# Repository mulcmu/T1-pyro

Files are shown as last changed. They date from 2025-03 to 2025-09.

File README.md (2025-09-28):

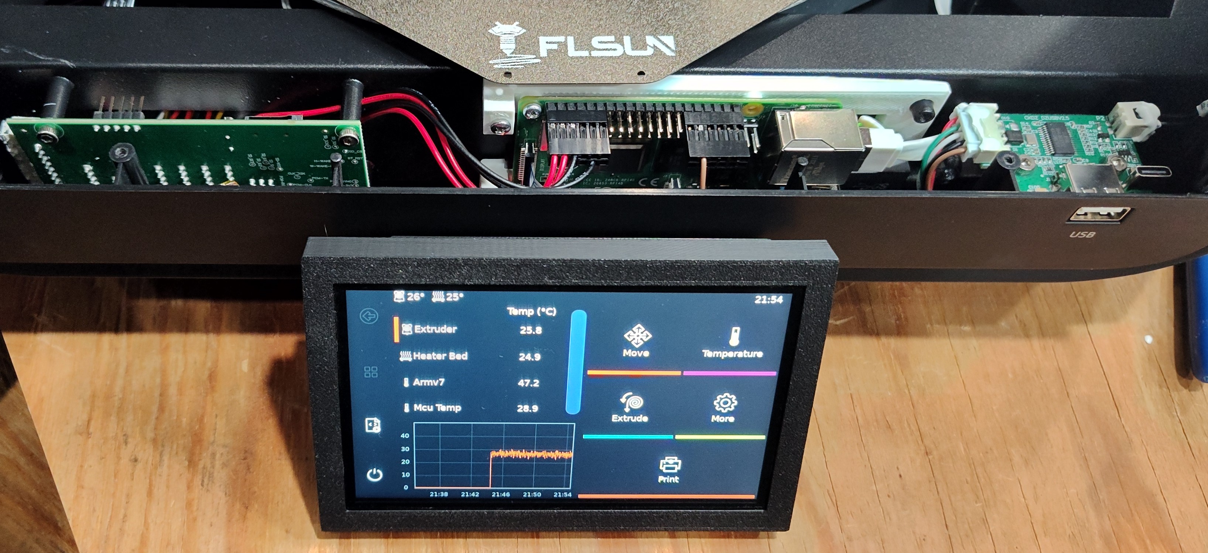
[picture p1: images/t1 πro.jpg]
./images/t1 πro.jpg


# T1 πro
Document and share progress to convert a FLSUN T1 Pro to T1 πro.

### Objectives

- Replace the stock host board (Core Board) with a Raspberry Pi
- Replace the stock screen with Fysetc Raspberry Pi 5 inch DSI Display
- Document stock hardware connections for troubleshooting/upgrades
- Reuse other stock hardware as much as practical
- Clean installation
- Up to date OS and Klipper [Ecosystem](https://klipper.discourse.group/t/klipper-architecture-ecosystem/6313)

### Current Status

* Pi 4 and the screen installed, fully operational
* Uses the stock 5v power supply on lower adapter board for Pi
* USB camera hub board reused by Pi
* Currently <u>irreversible</u> after flashing Klipper MCU hardware 
* [[load cell]](https://github.com/garethky/klipper/tree/load-cell-probe-community-testing) community testing branch working with stock lower function adapter board
  * `before: range 0.046875, average -0.420110, stDev 0.010482, average delta: 0.011671`
  * `  after: range 0.002557, average -0.304737, stDev 0.000692, average delta: 0.000532`

* Macros need a lot of work
* Help wanted, contributions welcomed

### Gen1/Gen2 Stock Hardware

My original T1 Pro was a Gen2, second T1 Pro purchased opened box was Gen1.  The Gen1 has older revision PCBs.  The Gen1 motherboard came with BTT stepper drivers vs FLSUN brand on Gen2.  BTT silk screen painted over in green even though the spare part clearly displayed the BTT marking on the website.  The Gen2 motherboard has some changes from the Gen1, Gen1 lacks the 5 pin firmware download header and a bunch of transistors under the steppers.  Gen1 has  some pin header jumpers under the steppers that are not on Gen2.  

The lower function adapter board on Gen1 has the low noise ADC chip bodged onto the back of the PCB and held with copious amounts of the white silastic.

The Gen2 CPAP fan aligned with the air hole opening in the top cover.  The Gen1 did not and sucked air in from inside the enclosure.

Gen1 also looks to have an older effector pcb, haven't taken that apart yet to document.

### Differences

* Fully open source Klipper ecosystem
* No power loss protection
* Ethernet connection possible, not just wifi
* Slightly bigger screen with more control
* Potential for Load cell probe accuracy improvements

### TODO

- [ ] Cleanup the printer.cfg file and macros
- [ ] Create Schematic (in progress)
- [X] Trace motor SPI connections
- [x] Document lower adapter board
- [x] Fix lower adapter board usart1 rx/tx
- [x] Document effector PCB and determine cable pinout
- [x] Document πro custom cables
- [X] Hotend thermistor noise at ambient temps
- [ ] Cleanup katapult installation
- [ ] Make a scripts for mcu fw compile and katapult deploy
- [X] moonraker [timelapse](https://github.com/mainsail-crew/moonraker-timelapse/blob/main/docs/installation.md)
- [ ] Document modifications to improve bed probe [performance](https://klipper.discourse.group/t/load-cell-probing-algorithm-testing/9751/102)
- [ ] Slay underbed dragons (potential regions were probe will not trigger as two load cells readings are exactly balanced out by 3rd load cell reading)
- [X] Modification for filament <u>movement</u> sensor
- [X] Better camera (mine broke already)
- [ ] Chamber temperature, RH, sensor
- [ ] Chamber heater support
- [ ] Improve boot speed of Pi
- [X] Does Pi need heatsinks or extra cooling - YES
- [ ] Overlay file system or similar to make more robust to power loss
- [ ] Installation guides
- [ ] Logo
- [ ] Standard preinstalled Pi image
- [ ] Redesign the screen bracket
- [ ] Find stock firmware for the motherboard MCU
- [x] Stock firmware for the probe MCU

### STL Models

Fusion360 models and STL located on pintables:

* https://www.printables.com/model/1191414-flsun-t1-pro-pi-and-screen-bracket
* https://www.printables.com/model/1282464-flsun-t1-alternate-camera
* https://www.printables.com/model/1401304-flsun-t1-vent-hole-drill-guide
* https://www.printables.com/model/1282464-flsun-t1-alternate-camera

### Custom Cables

* Custom cable from a Pi usb connector to the stock Usb hub board
* Custom cable from the stock lower adapter board 5v to the Pi *GPIO*
* [Details](custom_cables.md)

### Parts

* USB Extension cable for MCU ([Type A male to Type C female](https://www.amazon.com/dp/B07M999Y6T))
* Optional for Ethernet 
  * Low profile [connector cable](https://www.amazon.com/dp/B0D9JVSB2X?ref_=ppx_hzsearch_conn_dt_b_fed_asin_title_1) 
  * [Bulkhead connector](https://www.amazon.com/dp/B0D9JVSB2X)
* Industrial / rugged SD card for Pi
* SD card for flashing upper core board firmware
* ST Link v2 clone or similar [SWD debugger](https://github.com/WeActStudio/WeActStudio.MiniDebugger) (Required for [load_cell], recommended for katapult install on motherboard MCU)
* Some assorted M2, M2.5 and M3 screws are needed for assembly

### Installation

Current high level guide to implement:

* Get Pi setup and Klipper installed and tested before physical install into machine
* Print the brackets for printer installation
* Make the custom cables
* Remove stock host PCB (Core board) and screen
* Install Pi and 5" screen
* Flash Klipper firmware to motherboard
* [Optional for load cell] Modify lower function board with jumper and flash Klipper firmware to lower function board

Details:

* Fresh Bookworm Install:  Use Raspberry Pi Imager software to install Raspberry Pi OS Lite (64-bit)  to the SD card
    Current release is 2025-05-13.  Tested with 2024-11-19.

* Edit settings to set desired host name, password, and wifi configuration

* Modify the Pi config.txt

    ```
    # Uncomment some or all of these to enable the optional hardware interfaces
    dtparam=i2c_arm=on
    #dtparam=i2s=on
    #dtparam=spi=on
    
    # Enable audio (loads snd_bcm2835)
    dtparam=audio=on
    
    # Enable pwmchip sysfs interface
    dtoverlay=pwm-2chan,pin=12,func=4,pin2=13,func2=4
    
    # Automatically load overlays for detected cameras
    camera_auto_detect=0
    
    # Automatically load overlays for detected DSI displays
    display_auto_detect=1
    
    # Automatically load initramfs files, if found
    auto_initramfs=1
    
    # Don't have the firmware create an initial video= setting in cmdline.txt.
    # Use the kernel's default instead.
    disable_fw_kms_setup=1
    
    # Run in 64-bit mode
    arm_64bit=1
    
    # Disable compensation for displays with overscan
    disable_overscan=1
    
    # Run as fast as firmware / board allows
    arm_boost=1
    
    [cm4]
    otg_mode=1
    
    [cm5]
    dtoverlay=dwc2,dr_mode=host
    
    [all]
    enable_uart=1
    ```

> [!NOTE]
>
> Potential issues with touchscreen and [wifi firmware](https://github.com/KlipperScreen/KlipperScreen/discussions/1491).  I did not encounter any issues with the wifi.
>
> ``` Remove problematic wifi
> sudo apt remove firmware-brcm80211
> sudo apt-mark hold firmware-brcm80211
> sudo reboot now 
> ```

* First boot, use SSH or usb keyboard to update

  ``` 
  sudo apt update
  sudo apt upgrade
  sudo systemctl disable systemd-networkd-wait-online.service
  sync
  sudo reboot now
  ```

* Install ts_lib for touch calibration

  ```
  sudo apt-get install libts-bin
  sudo ts_calibrate
  sudo ts_test
  sync
  sudo reboot now
  ```

* Install Git, KIAUH, Klipper, moonraker, mainsail, klipperscreen, crowsnest, klipper-backup, 

    ```
    sudo apt-get install git
    cd ~ 
    git clone https://github.com/dw-0/kiauh.git
    ./kiauh/kiauh.sh
    ```

* Optional for [load_cell] support: switch to load-cell-probe-community-testing fork

    ```	
    echo "For KIAUH v5"
    cd ~/kiauh
    nano klipper_repos.txt
    
    echo "For KIAUH v6"
    cp default.kiauh.cfg kiauh.cfg
    nano kiauh.cfg
    ```

	add this to file and save:

   ```
   https://github.com/garethky/klipper,load-cell-probe-community-testing
   ```

	switch klipper branch in kiauh to the load cell testing repository

* Install extra python packages for Measuring Resonances and Load_Cell

  ```
  sudo apt install python3-numpy python3-matplotlib libatlas-base-dev libopenblas-dev python3-scipy python3-serial
  ~/klippy-env/bin/pip install -v "numpy<1.26"
  ~/klippy-env/bin/pip install -v "scipy"
  ```

* Optional for [load_cell] support: Setup load cell [probe debug tool](https://observablehq.com/@garethky/klipper-load-cell-debugging-tool)

* Install ST-Link

  ```
  sudo apt install gcc build-essential cmake libusb-1.0-0 libusb-1.0-0-dev libgtk-3-dev pandoc -y
  cd ~ 
  git clone https://github.com/stlink-org/stlink.git
  cd stlink
  make clean && make release
  sudo make install
  sudo ldconfig
  ```

* Install katapult

    ```
    cd ~
    git clone https://github.com/Arksine/katapult
    ```

* Install timelapse

    ```
    cd ~/
    git clone https://github.com/mainsail-crew/moonraker-timelapse.git
    cd ~/moonraker-timelapse
    make install
    
    ```

    ```
    # moonraker.conf
    
    [update_manager timelapse]
    type: git_repo
    primary_branch: main
    path: ~/moonraker-timelapse
    origin: https://github.com/mainsail-crew/moonraker-timelapse.git
    managed_services: klipper moonraker
    ```

* No login shell (required for load_cell) and Wifi enabled (optional)

    ``` 
    sudo raspi-config
    ```

    * Setup wifi under System Options
    * Select wifi country in Localizations Options
    * Enable serial uart, no console
      * Interface options
      * Serial Port
      * No login shell
      * Yes hardware enabled
    ```
    sudo nmtui
    ```

    * Check wifi setup and add additional networks if desired

* Enable host mcu
  * Setup hardware PWM using this guide https://www.klipper3d.org/RPi_microcontroller.html
  
  * The case light gets connected to PWM0 with it routed it to gpio12.
  
  * /etc/rc.local will need to be created, don't forget the #! and chmod +x
  
    ```
    #!/bin/sh -e
    
    # Enable pwmchip sysfs interface
    echo 0 > /sys/class/pwm/pwmchip0/export
    echo 1 > /sys/class/pwm/pwmchip0/export
    
    exit 0
    ```

* Modify printer.cfg
  * Copy the printer.cfg from this repository and update with your existing calibration (endstops, bedmesh, PID, etc)
  * or.. edit your printer.cfg to remove all the FLSUN additions

* Build motherboard MCU firmware

    ```
    sudo service klipper stop
    cd ~
    cd klipper
    make clean
    cp ~/motherboard.menu.config .config
    make menuconfig
    make
    cp out/klipper.elf ~/motherboard.elf
    cp out/klipper.bin ~/motherboard.bin
    ./scripts/update_mks_robin.py out/klipper.bin ~/Robin_nano35.bin
    cp .config ~/motherboard.menu.config
    sudo service klipper start
    ```

> [!NOTE]
>
> Motherboard MCU menuconfig settings:
>
> * Enable extra low-level configuration options
> * Micro-controller Arch (STM32)
> * Processor model (STM32F103)
> * Bootloader offset (28KiB Bootloader) for SD card flash
> * Bootloader offset (8KiB bootloader) for Katapult
> * Clock Reference (8 MHz)
> * Communication interface (Serial (on USART3 PB11/PB10))
> * (250000) Baud for serial port
> * Enable step on both edges
> * PE8 (pins at startup for heatsink cooling fan until klipper boots)

> [!NOTE]
>
> The Robin_nano35.bin is only for using on SD card with motherboard stock bootloader.

* Optional for load cell support: Build lower function adapter board MCU firmware

  ```
  sudo service klipper stop
  cd ~
  cd klipper
  make clean
  cp ~/load_cell.menu.config .config
  make menuconfig
  make
  cp out/klipper.elf ~/load_cell.elf
  cp out/klipper.bin ~/load_cell.bin
  cp .config  ~/load_cell.menu.config
  sudo service klipper start
  ```

> [!NOTE]
>
> Load Cell MCU menuconfig settings:
>
> * Enable extra low-level configuration options
>
> * Micro-controller Arch (STM32)
>
> * Processor model (STM32F103)
>
> * Bootloader offset (8KiB Bootloader)
>
> * Clock Reference (8 MHz)
>
> * Communication interface (Serial (on USART1 PA10/PA9))
>
> * (250000) Baud for serial port
>
>   

* Build Katapul bootloaders

```
sudo service klipper stop
cd ~
cd katapult
make menuconfig
make clean
make
cp out/katapult.elf ~/mb_katapult.elf
cp out/katapult.bin ~/mb_katapult.bin
sudo service klipper start
```

> [!NOTE]
>
> * Micro-controller Arch (STM32)
> * Processor model (STM32F103)
> * Deployment app (Do not build)
> * Clock Reference (8 MHz)
> * Communication interface (Serial (on USART3 PB11/PB10))
> * Application start offset (8KiB bootloader)
> * (250000) Baud for serial port
> * (!PD12) Status LED:  Optional will turn on led by SD card but will direct short if an SD card is inserted!!!

```
sudo service klipper stop
cd ~
cd katapult
make menuconfig
make clean
make
cp out/katapult.elf ~/lc_katapult.elf
cp out/katapult.bin ~/lc_katapult.bin
sudo service klipper start
```

> [!NOTE]
>
> * Micro-controller Arch (STM32)
> * Processor model (STM32F103)
> * Deployment app (Do not build)
> * Clock Reference (8 MHz)
> * Communication interface (Serial (on USART1 PA10/PA9))
> * Application start offset (8KiB bootloader)
> * (250000) Baud for serial port

* Make custom cables

* Print custom brackets

* Install pi in custom bracket (four M2.5x6 screws)

* Install screen in custom bracket

* Remove the stock screen, host (core board) PCB, ribbon cable on lower adapter board, power cable from lower adapter board, cable from the usb hub

* Optional for load cell support:

    * Remove the J20 5 pin header pins and replace with right angle head pins on bottom of pcb if room

    * A magnet/enamel wire needs added to jumper Pin 30 on STM32F103 to Pin 32

* Install the PI, slide over existing standoffs, secure with two M3x6 screws

* Connect usb adapter extension from pi to the usb cable running to upper adapter board / motherboard

* Connect custom usb hub cable to pi usb and gpio

* (Optional) Connect ethernet cable and fit the bulkhead adapter somewhere.

* Connect the custom power cable from lower adapter board to GPIO

* Initial test, at this point pi and screen should boot when printer turned on.  Klipperscreen should load and show *MCU Protocol Error*.  The MCU firmware needs to be updated (or potentially Klipper downgraded) to be be compatible.

> [!WARNING]
>
> After flashing the Klipper MCU firmware returning printer to original stock configuration is not possible!
* Flash motherboard MCU
  * Copy the ~/klipper/out/Robin_nano35.bin file to an empty fat32 formatted sd card
  * With printer powered off, install the sd card in the motherboard
  * Power on printer and wait 30 seconds
  * Power off printer and remove the sd card
  * Robin_nano35.bin should be renamed to Robin_nano35.cur

* Optional for [load_cell] support: Use ST-Link v2 programmer or similar to flash the load_cell.bin firmware to the STM32
  * Configure [openocd](https://openocd.org/), [stlink tools](https://github.com/stlink-org/stlink), or similar for your programming adapter and OS
  * Connect STLINK v2 adapter to JTAG port on lower function adapter board
  * Save a copy of the existing firmware `st-flash read out.bin 0x0800000 0x20000`
  * Write the load_cell.bin file to the MCU `st-flash write load_cell.bin 0x08000000`

### TODO: katapult stuff

```

sudo service klipper stop
python3 ~/katapult/scripts/flashtool.py --request-bootloader -d /dev/serial/by-id/usb-1a86_USB_Serial-if00-port0
python3 ~/katapult/scripts/flashtool.py -d /dev/serial/by-id/usb-1a86_USB_Serial-if00-port0 -f ~/motherboard.bin
sudo service klipper start

sudo service klipper stop
python3 ~/katapult/scripts/flashtool.py --request-bootloader -d /dev/ttyS0
python3 ~/katapult/scripts/flashtool.py -d /dev/ttyS0 -f ~/load_cell.bin
sudo service klipper start

st-flash erase
st-flash write mb_katapult.bin 0x08000000
st-flash write motherboard.bin 0x08002000

st-flash erase
st-flash write lc_katapult.bin 0x08000000
st-flash write load_cell.bin 0x08002000

host MCU update
sudo service klipper stop
make flash
sudo service klipper start

```

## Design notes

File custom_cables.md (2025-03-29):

To build these cables you need crimpers for Dupont and JST XH terminals, terminals to crimp and the housings.

https://www.amazon.com/YMYP-JST-XH-0-25-1-5mm%C2%B2-JST-SM2-54-Connector/dp/B0C6DKZC4K/ 

https://www.amazon.com/WOWOONE-620pcs-Connector-Housing-Terminal/dp/B0897KGG59/

### Cable from Pi USB to stock USB hub board

The camera and external usb stock pcb uses a usb hub IC.  There is also a transistor circut to power the case light on and off.  The 5 pin 2.54 JST XH connector needs to be wired to one of the Pi's usb ports and the control line for the light connected to the PI GPIO header.

Usb breakout pcb

https://www.amazon.com/MakerHawk-Adapter-Converter-Interface-Breakout/dp/B07MBSTZYG

https://www.amazon.com/Teansic-Breakout-Adapter-2-54mm-Module/dp/B09ZNK2Q5L

Connections

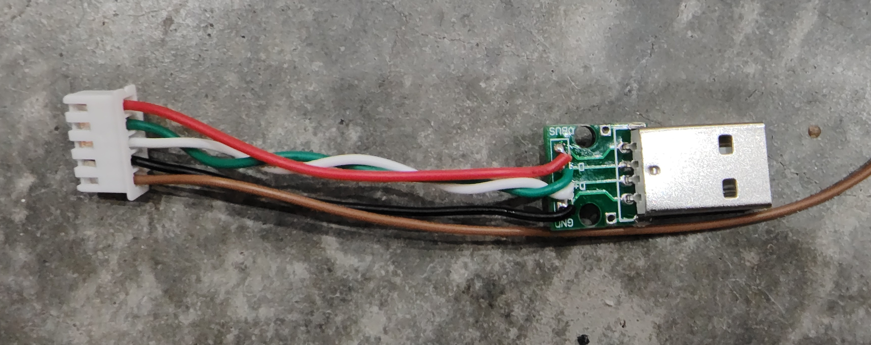
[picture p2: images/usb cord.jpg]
./images/usb cord.jpg


The brown wire goes off to the GPIO Dupont connector.

Use some heat shrink tubing to clean up/protect the usb pcb

Green and white data lines twisted for good measure

### Power Cable

The lower core board has a 5v supply that powered the original motherboard.  There is not enough room to power the Pi via the usb connector when installed so it needs to be powered by the GPIO header.

One side has another 5 pin 2.54 JST XH connector.  The other side needs dupont terminals.  A double row dupont connector 2x6 is recommended for convivence and to keep from messing up the connections.

Two red wires are the 5v and two black wires are the common.

Connections

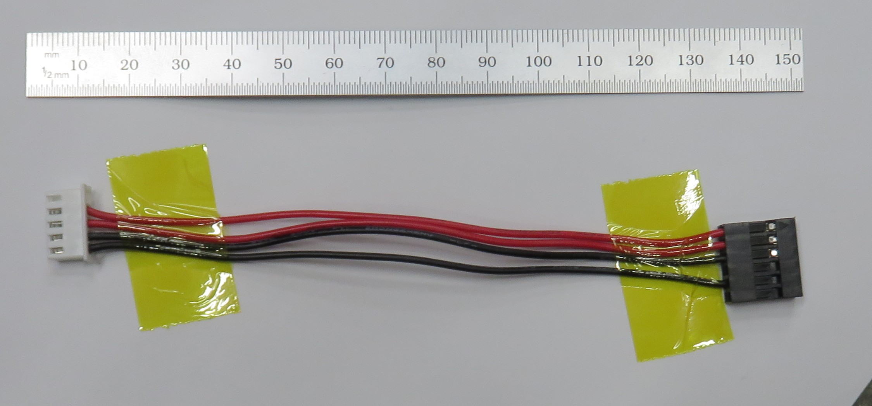
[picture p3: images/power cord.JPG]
./images/power cord.jpg


Optional for [load cell] support:

Two wires need run from the PI GPIO RX/TX to the modified lower function adapter board.  These wires terminate in a separate 5 pin Dupont housing.

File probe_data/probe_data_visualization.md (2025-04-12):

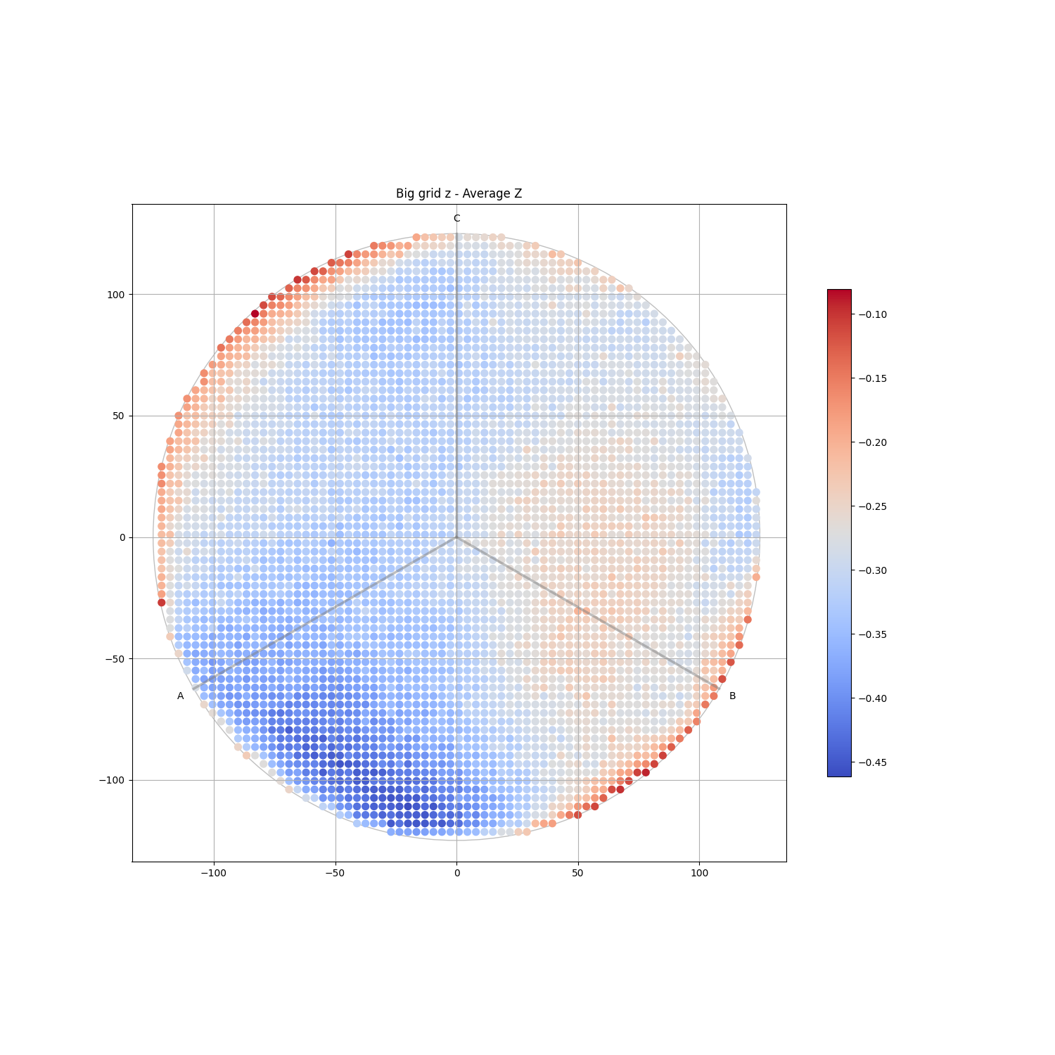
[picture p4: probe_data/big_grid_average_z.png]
Big grid z - Average Z


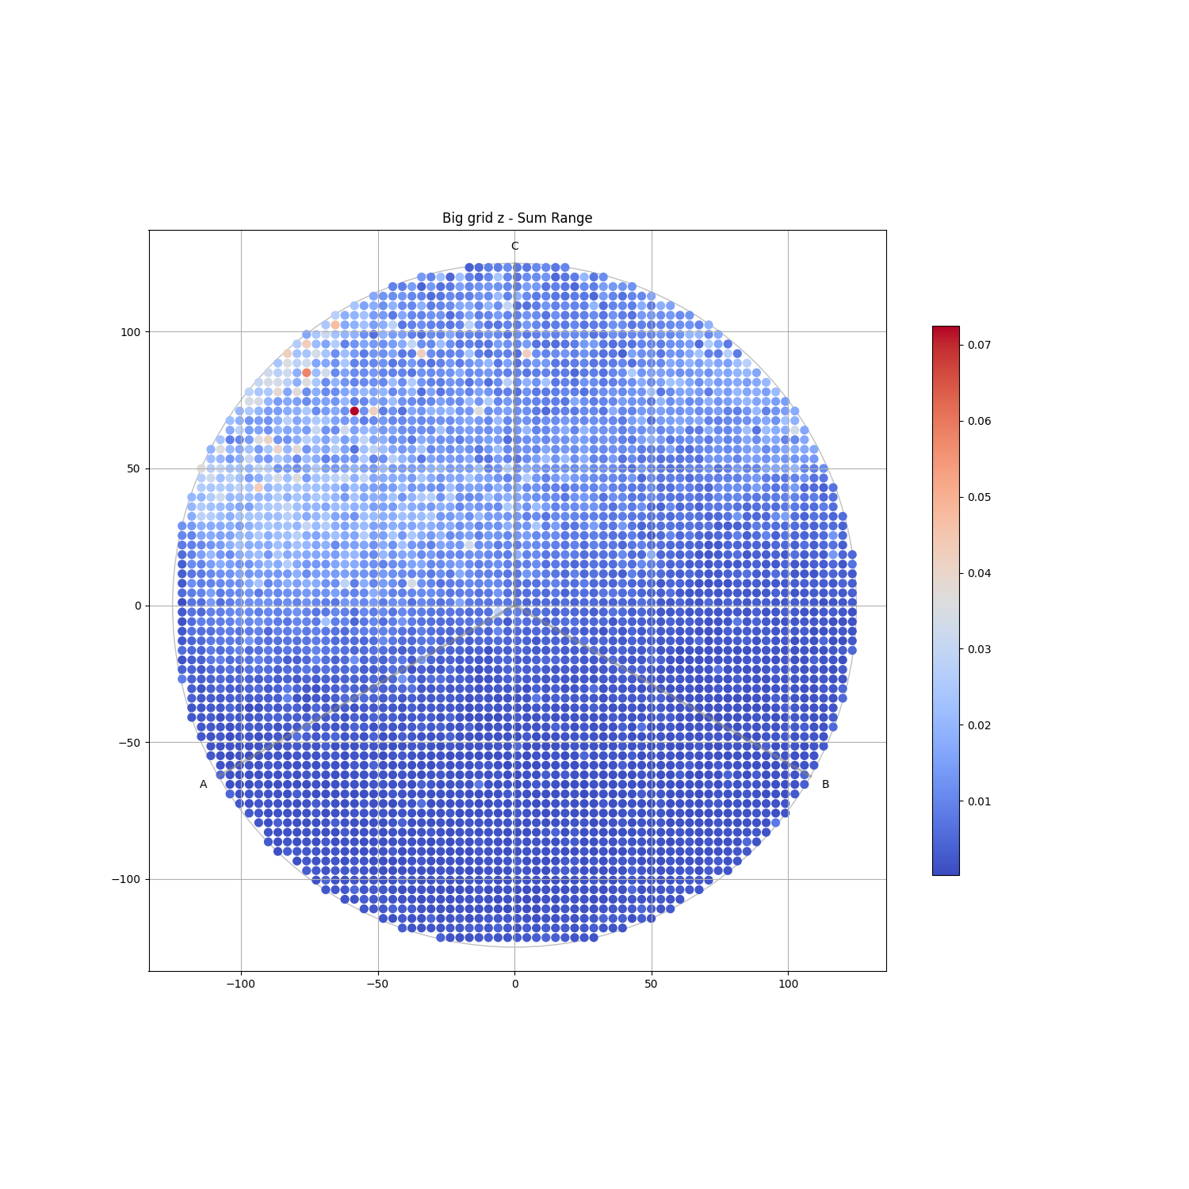
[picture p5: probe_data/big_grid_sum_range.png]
Big grid z - Sum Range


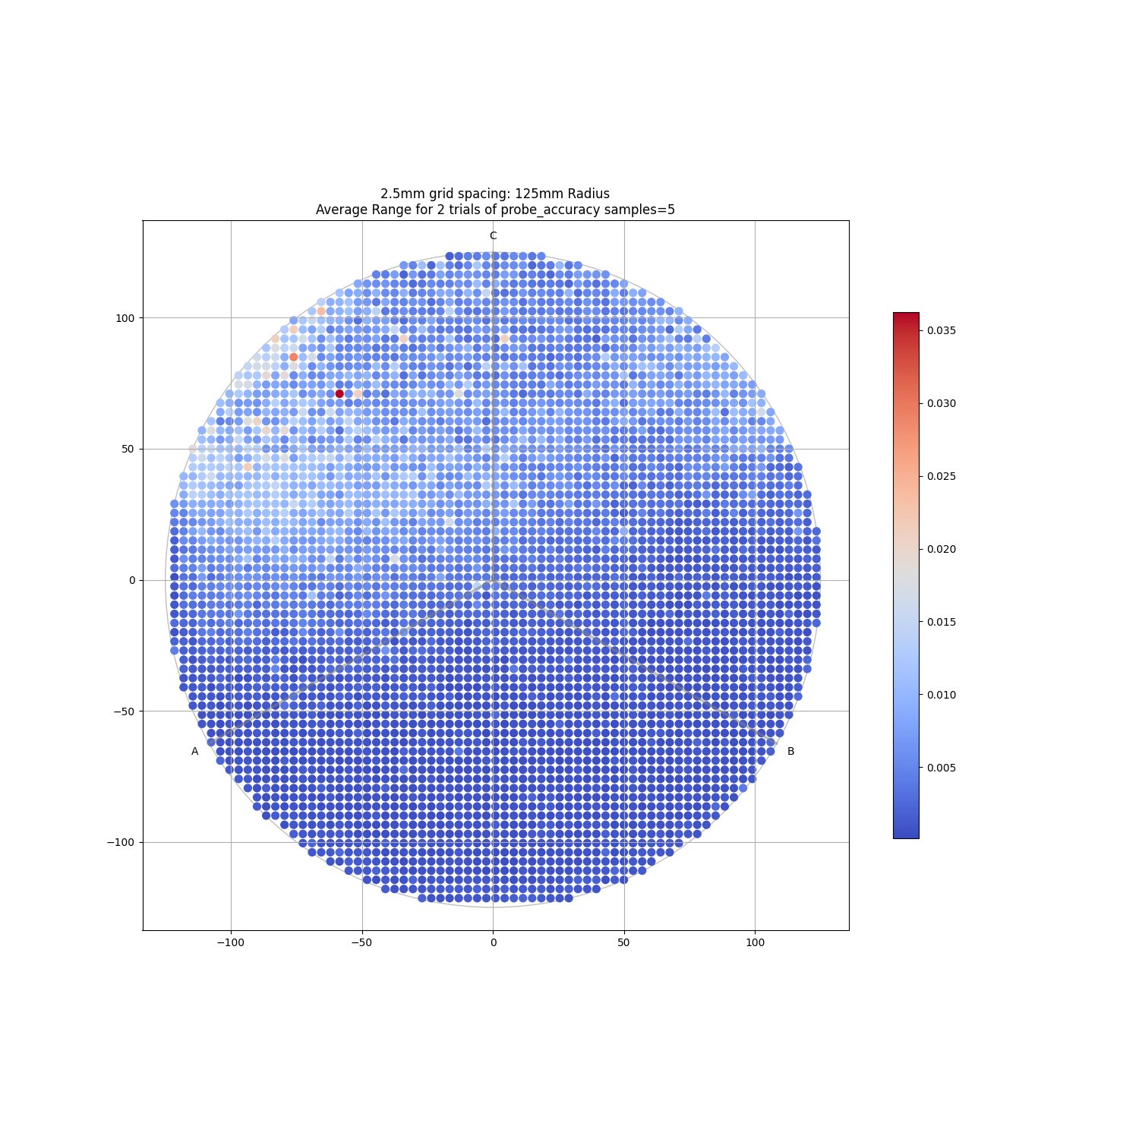
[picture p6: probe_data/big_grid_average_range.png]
2.5mm grid spacing: 125mm Radius Average Range for 2 trials of probe_accuracy samples=5


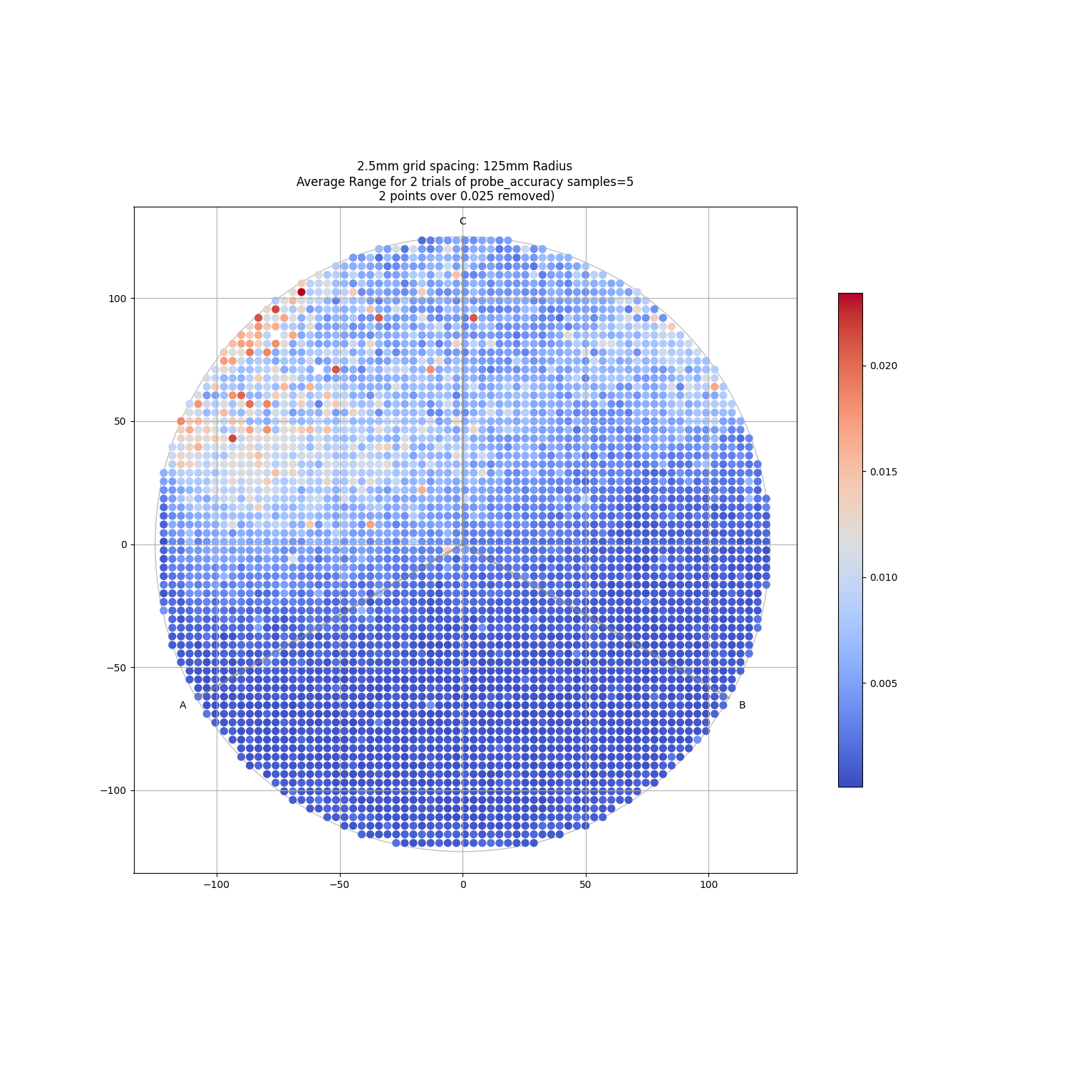
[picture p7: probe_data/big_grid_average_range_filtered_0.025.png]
2.5mm grid spacing: 125mm Radius Average Range for 2 trials of probe_accuracy samples=5 points over 0.025 removed


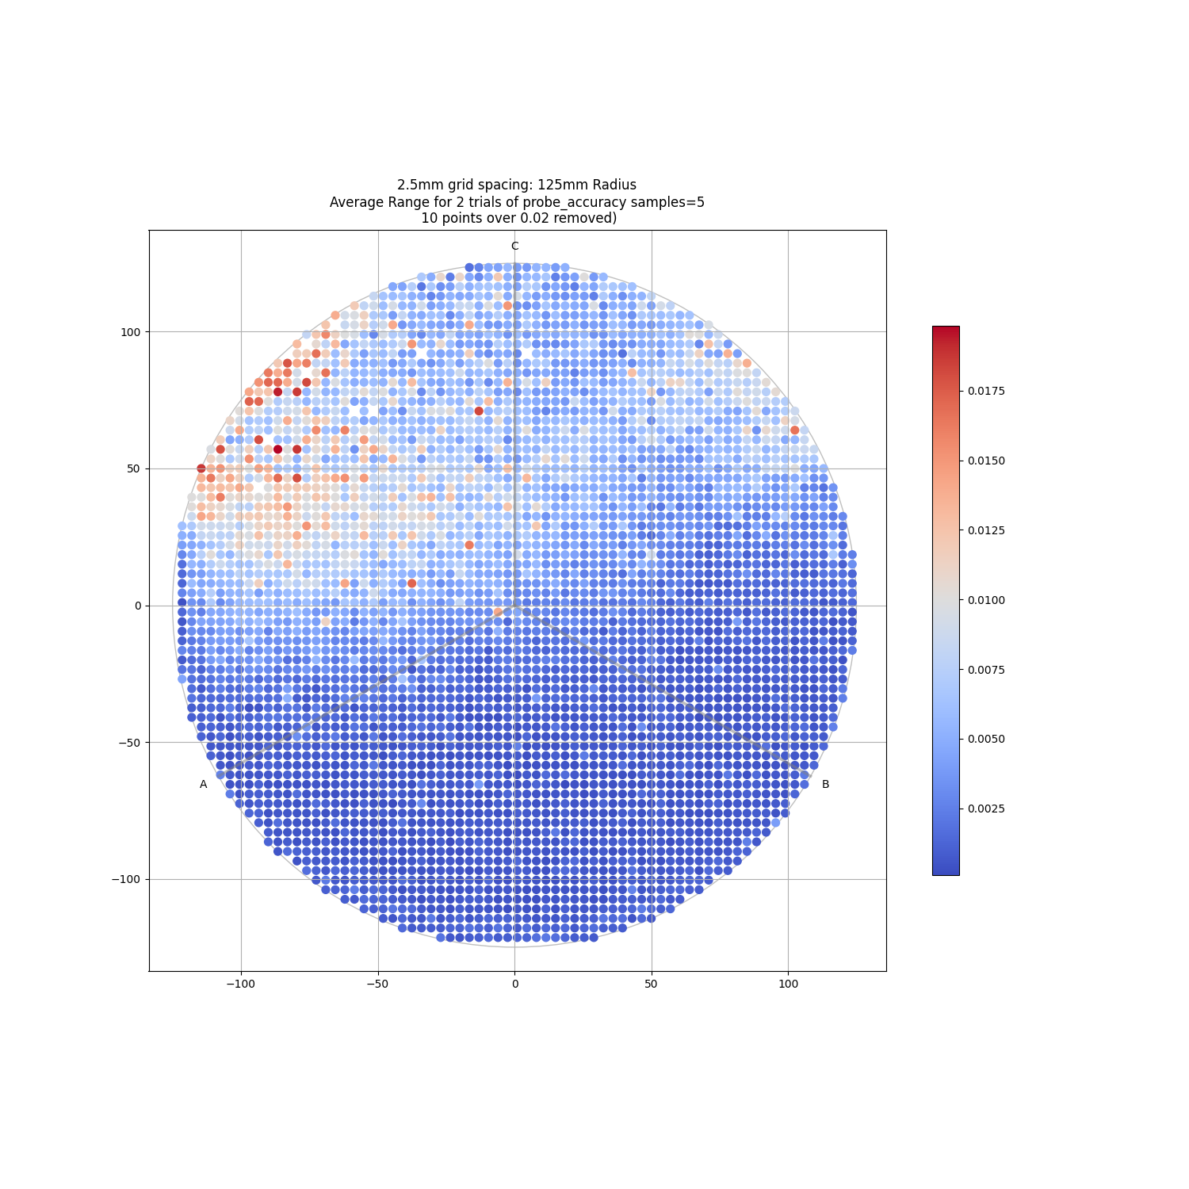
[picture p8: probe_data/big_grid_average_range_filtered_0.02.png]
2.5mm grid spacing: 125mm Radius Average Range for 2 trials of probe_accuracy samples=5 points over 0.02 removed


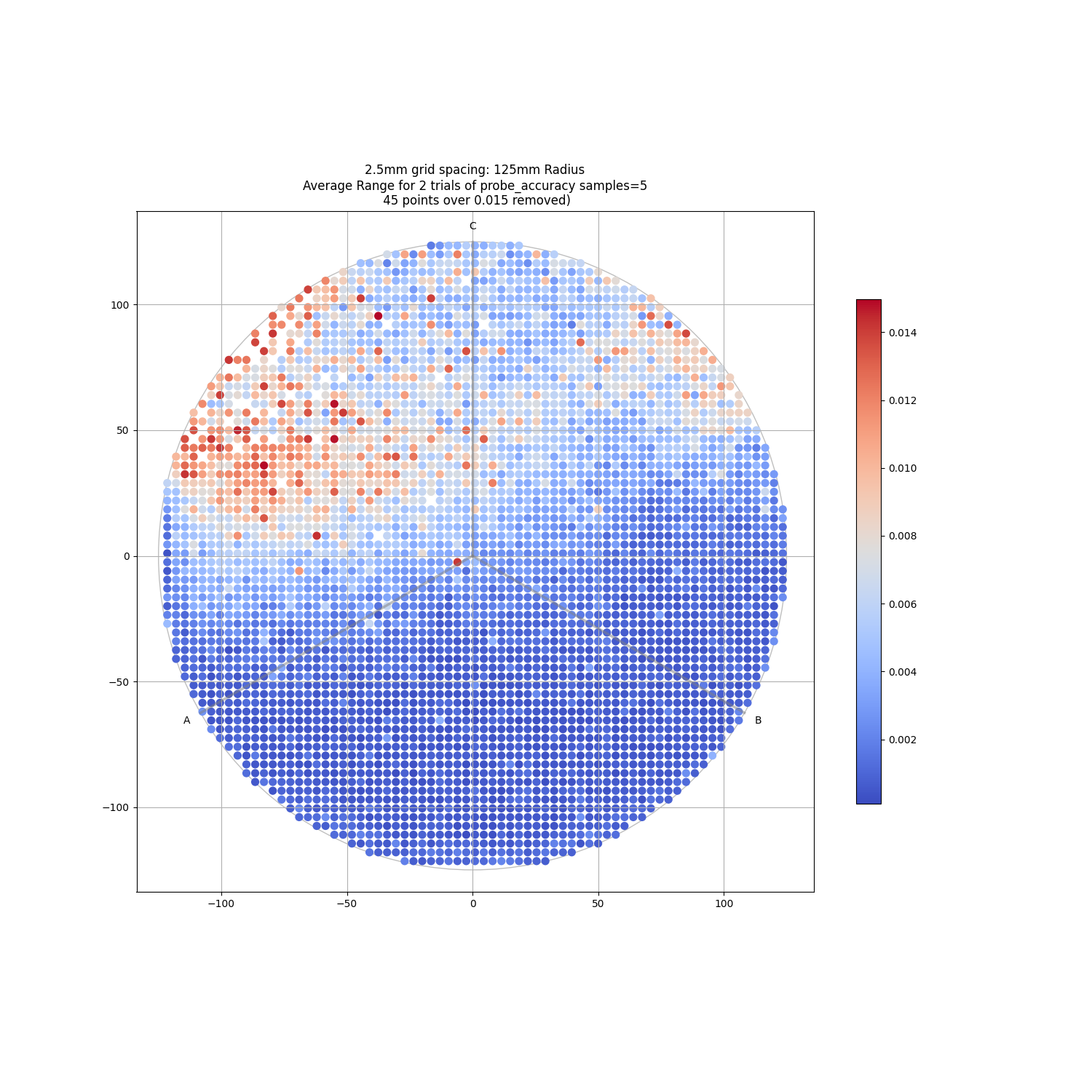
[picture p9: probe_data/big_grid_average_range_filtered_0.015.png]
2.5mm grid spacing: 125mm Radius Average Range for 2 trials of probe_accuracy samples=5 points over 0.015 removed


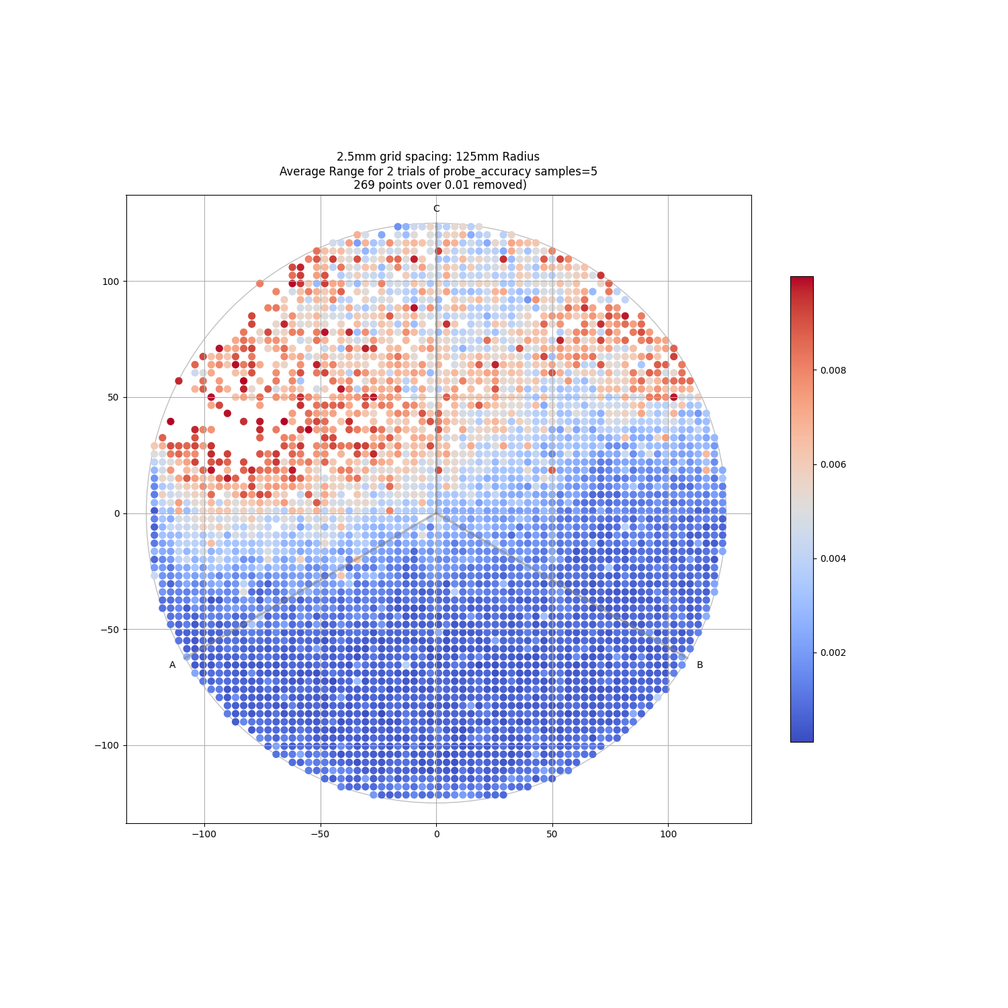
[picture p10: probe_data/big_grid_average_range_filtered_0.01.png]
2.5mm grid spacing: 125mm Radius Average Range for 2 trials of probe_accuracy samples=5 points over 0.01 removed


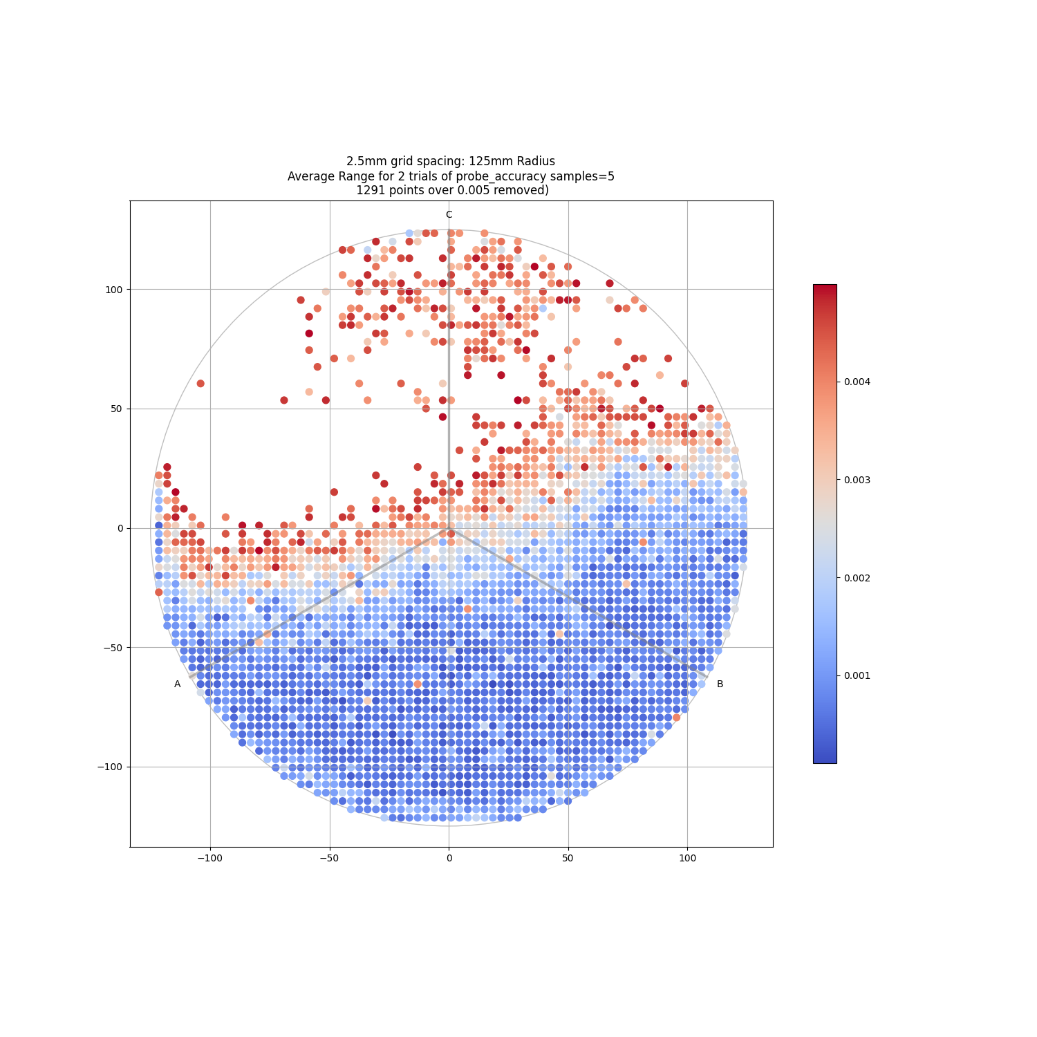
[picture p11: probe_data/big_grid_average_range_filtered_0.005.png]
2.5mm grid spacing: 125mm Radius Average Range for 2 trials of probe_accuracy samples=5 points over 0.005 removed


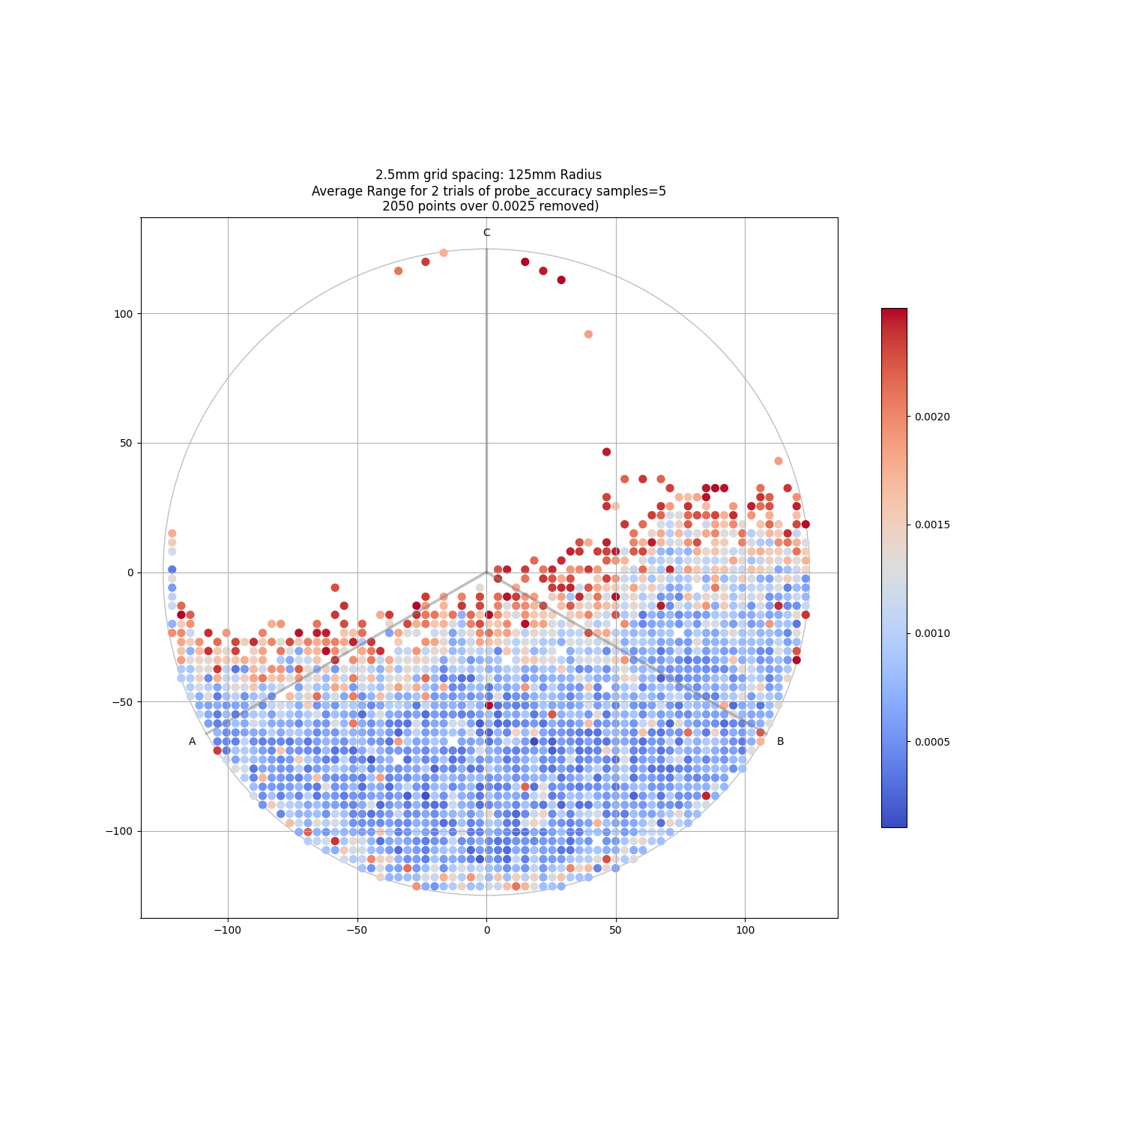
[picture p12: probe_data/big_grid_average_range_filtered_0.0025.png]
2.5mm grid spacing: 125mm Radius Average Range for 2 trials of probe_accuracy samples=5 points over 0.0025 removed


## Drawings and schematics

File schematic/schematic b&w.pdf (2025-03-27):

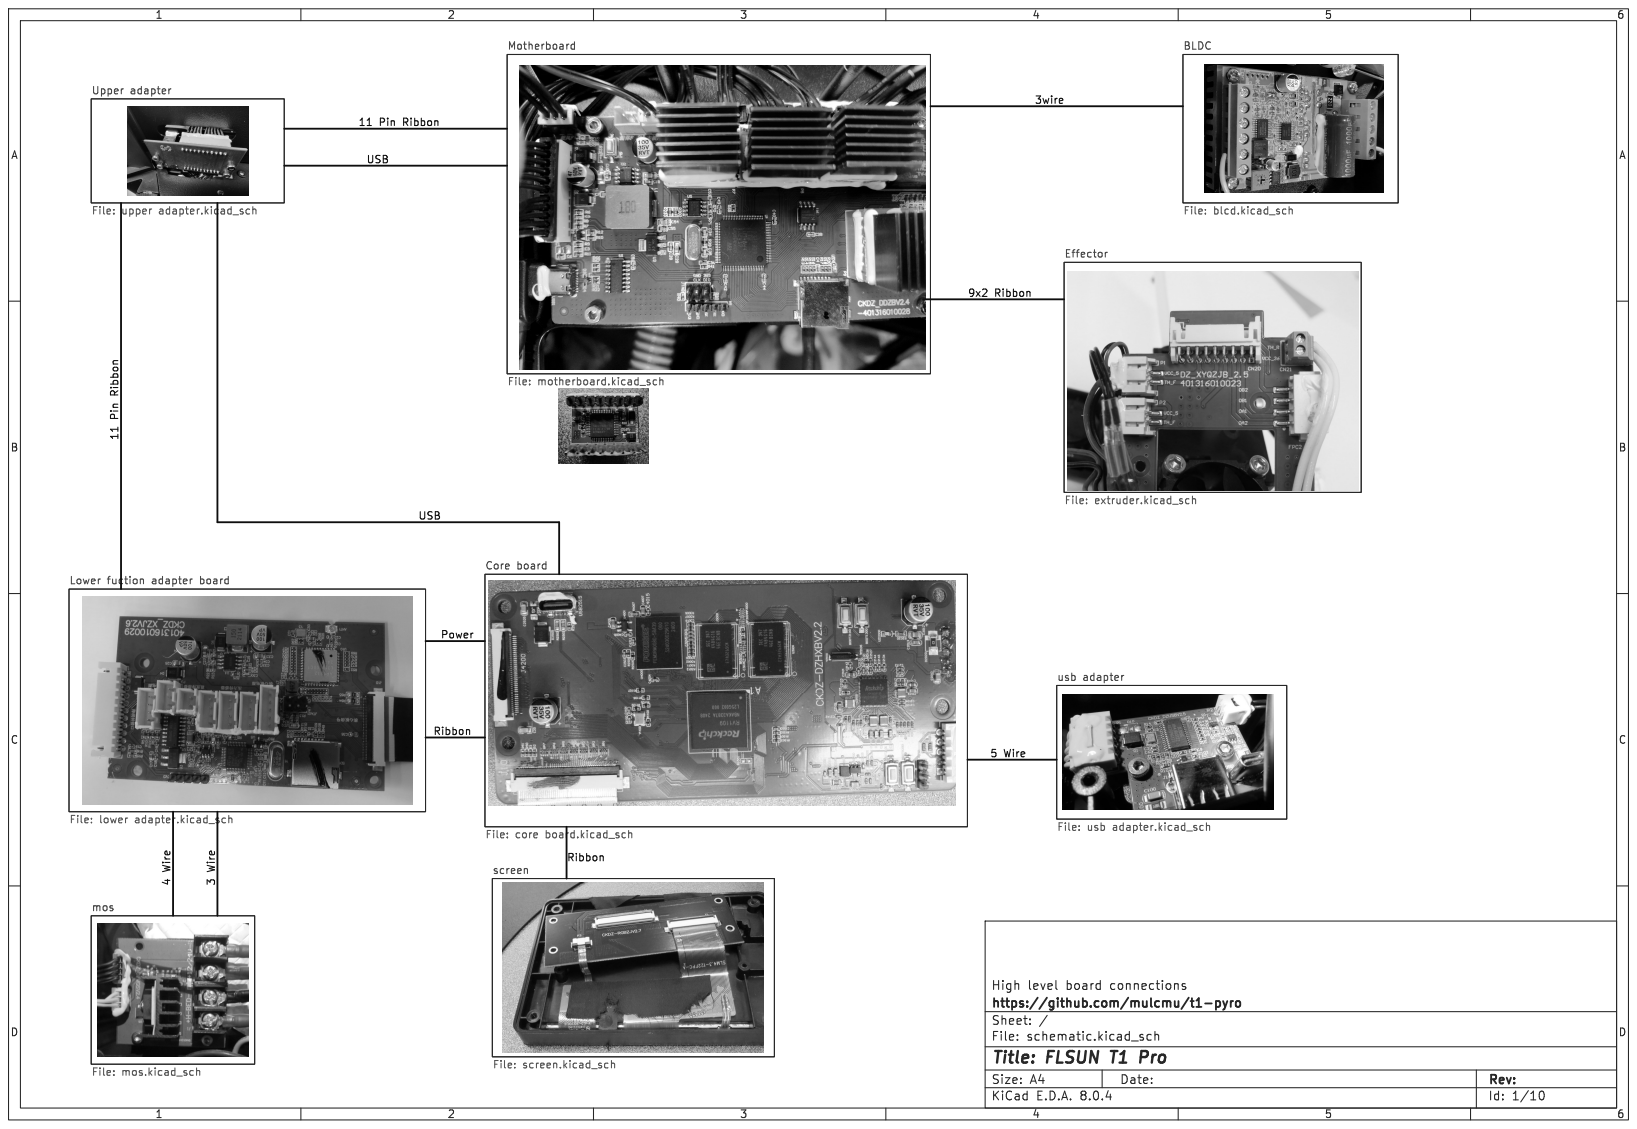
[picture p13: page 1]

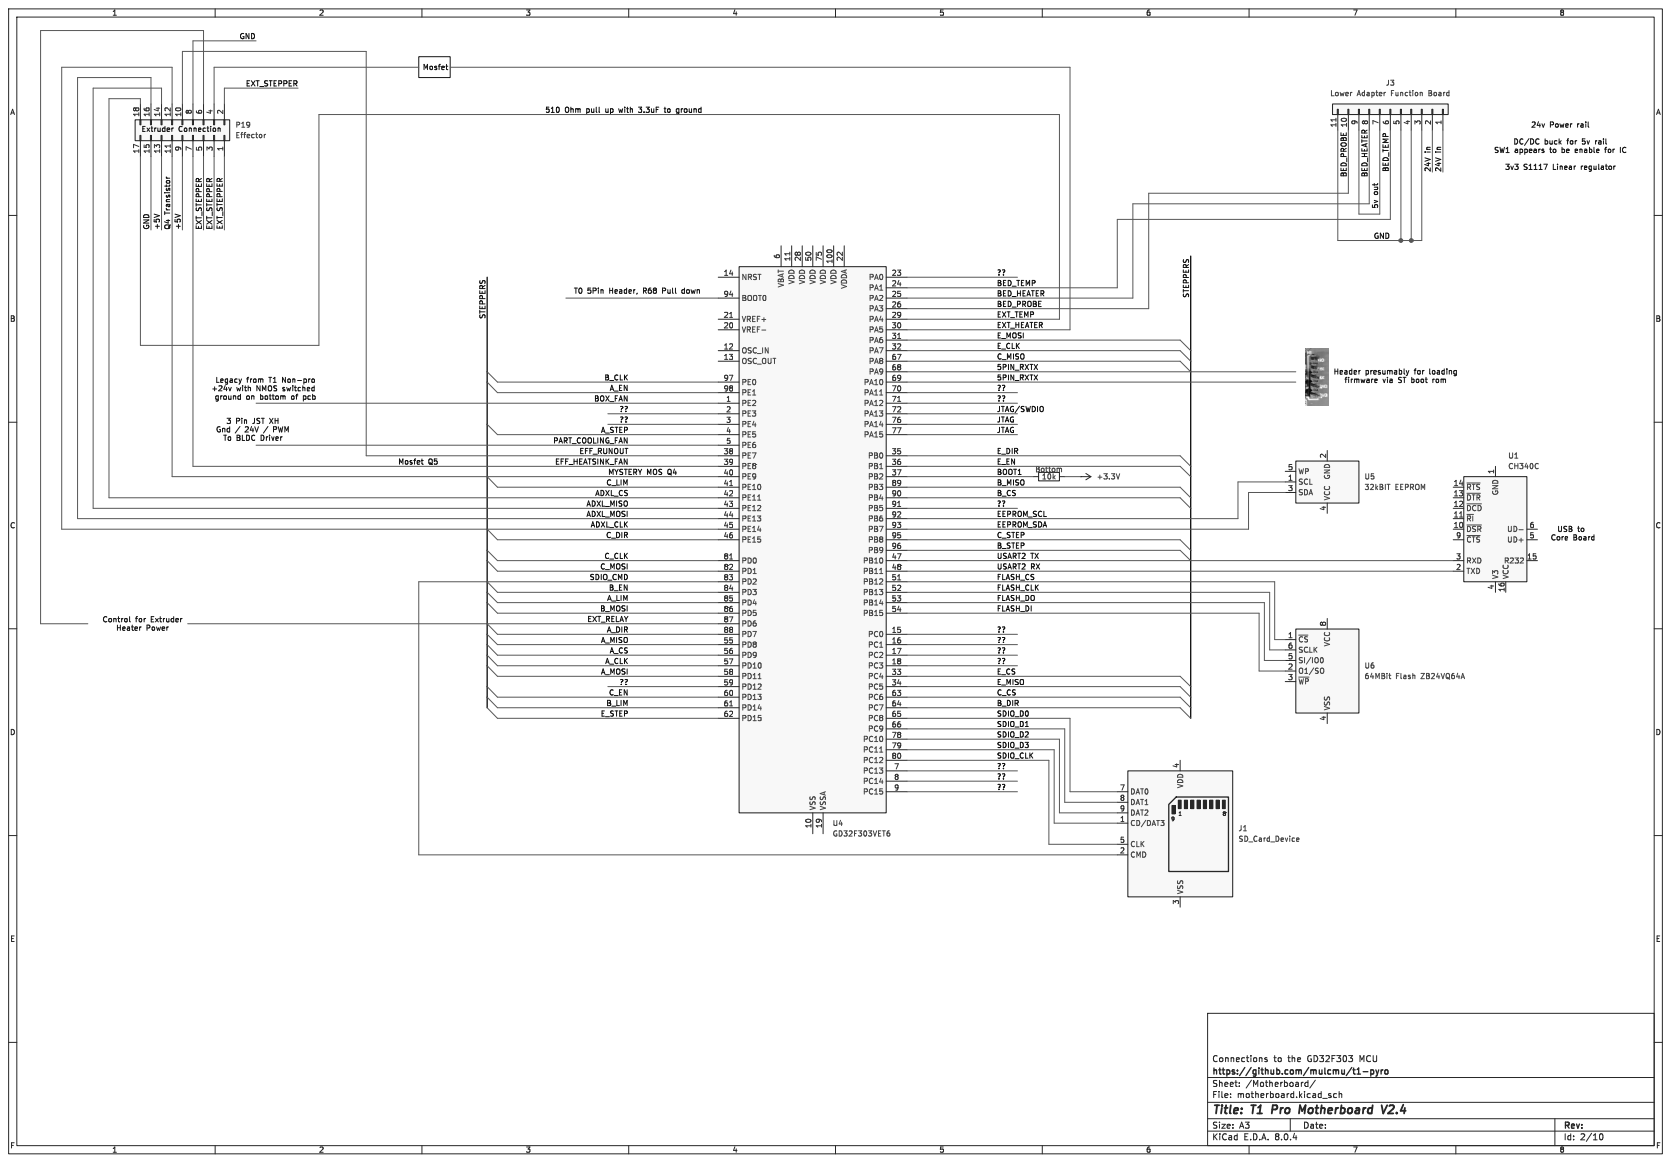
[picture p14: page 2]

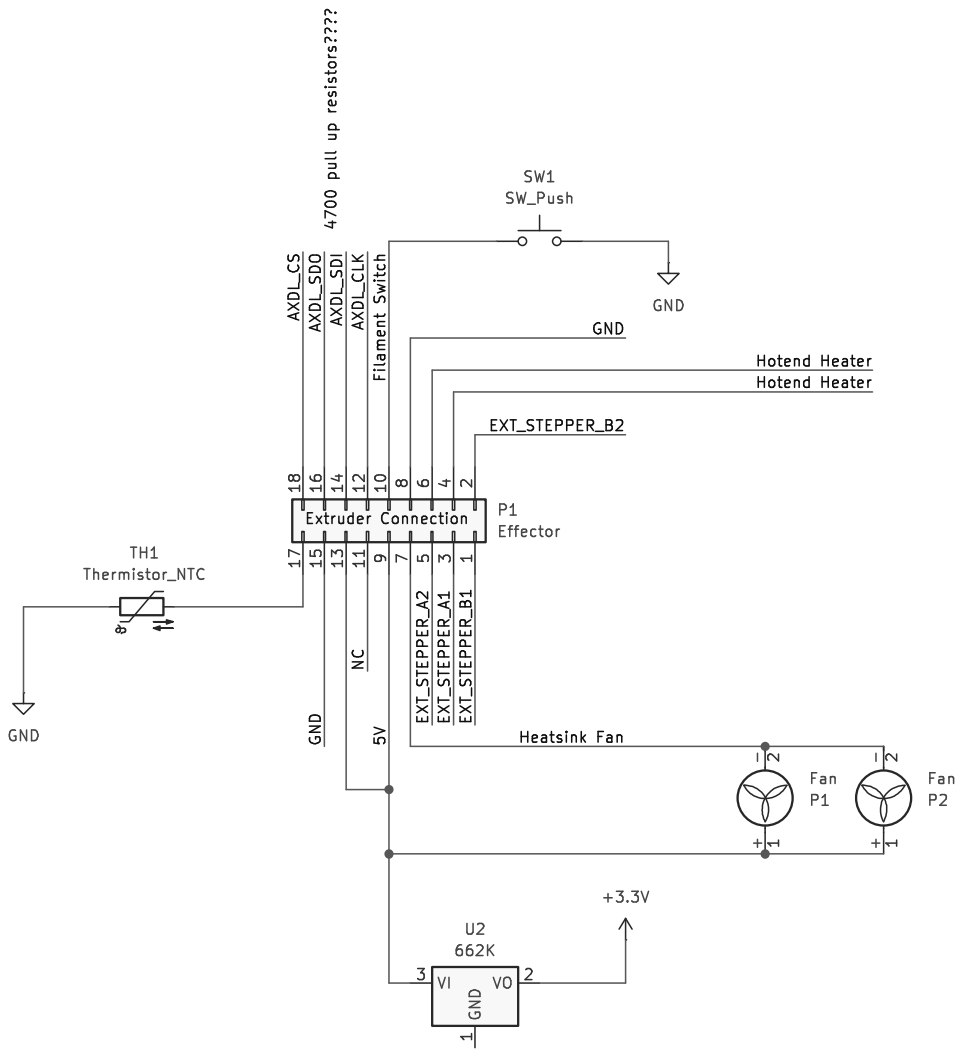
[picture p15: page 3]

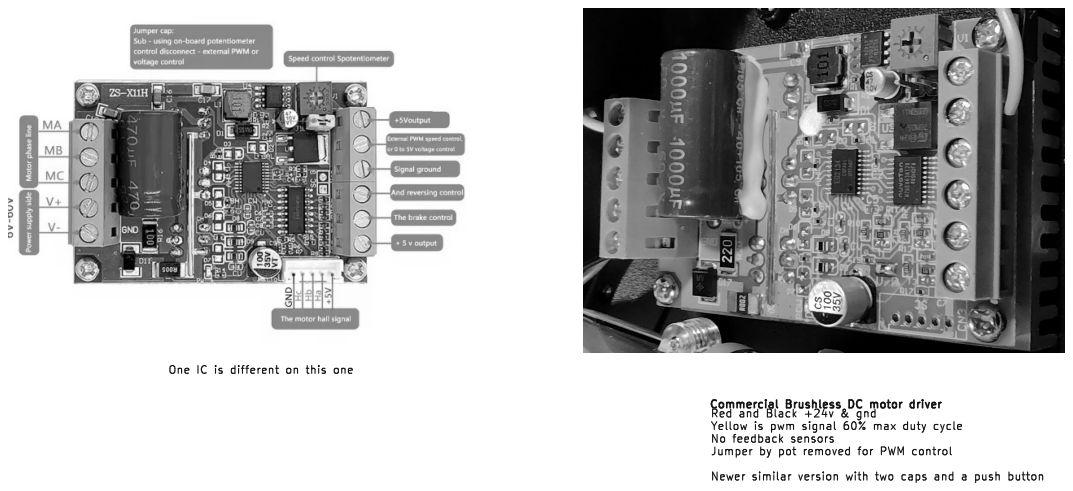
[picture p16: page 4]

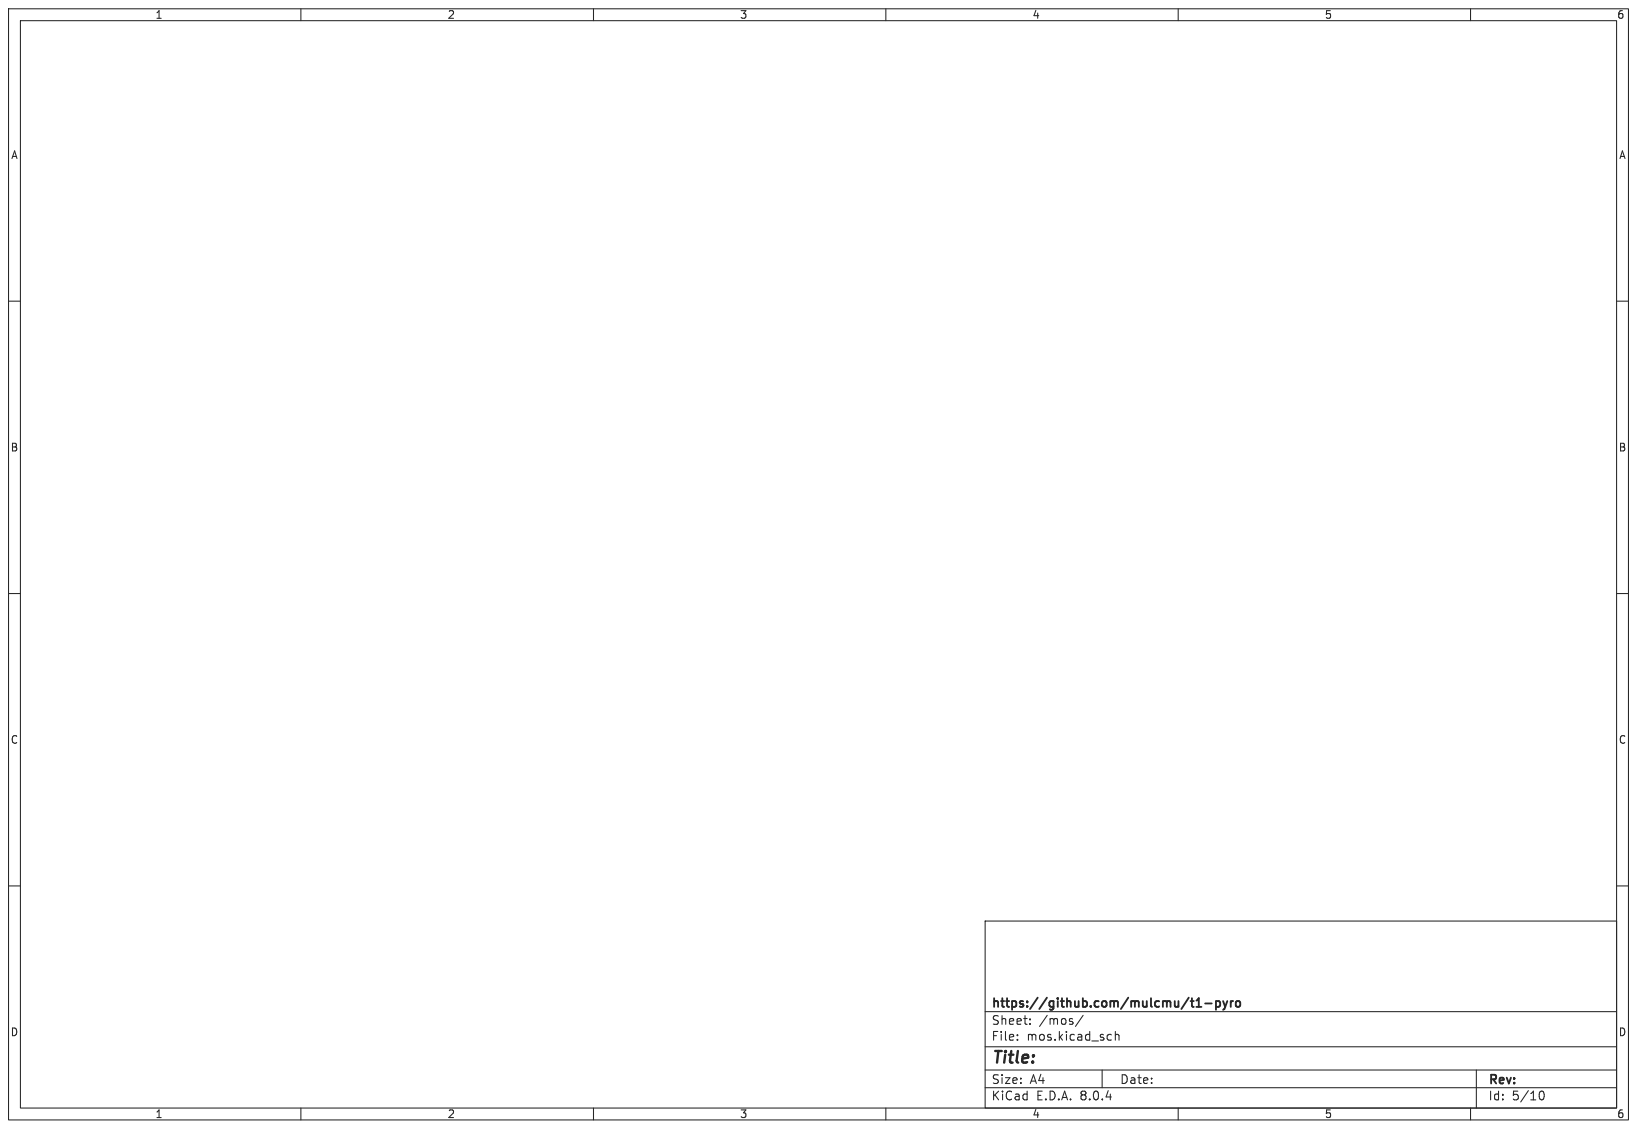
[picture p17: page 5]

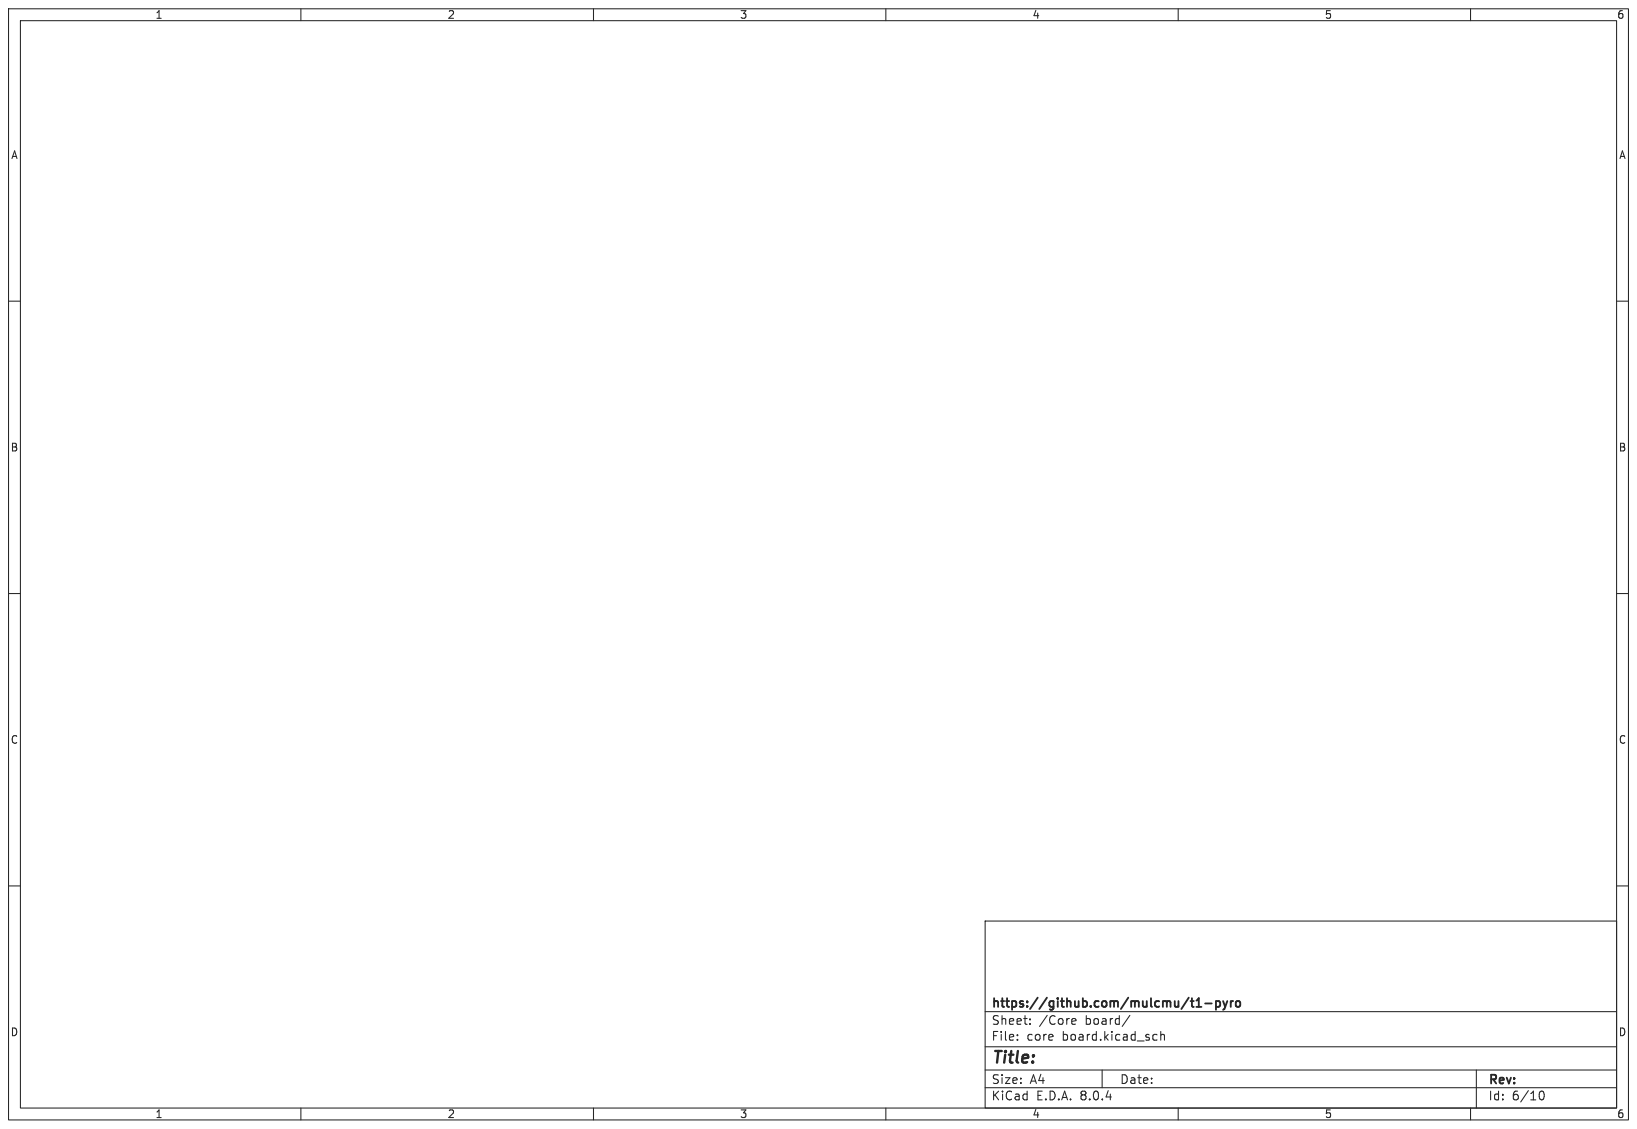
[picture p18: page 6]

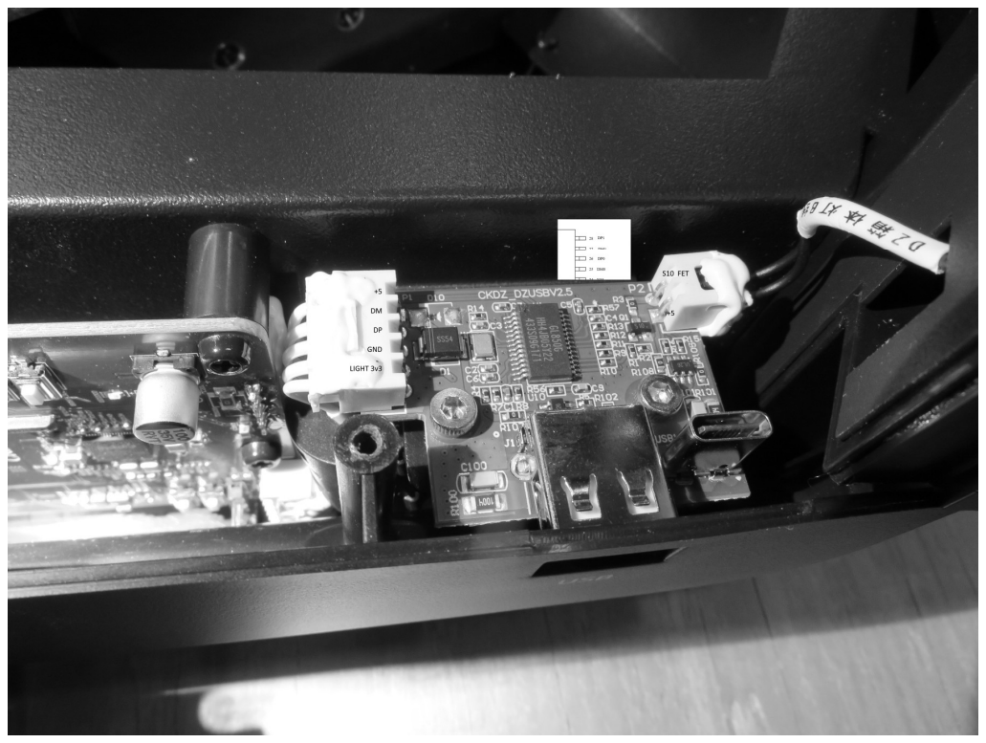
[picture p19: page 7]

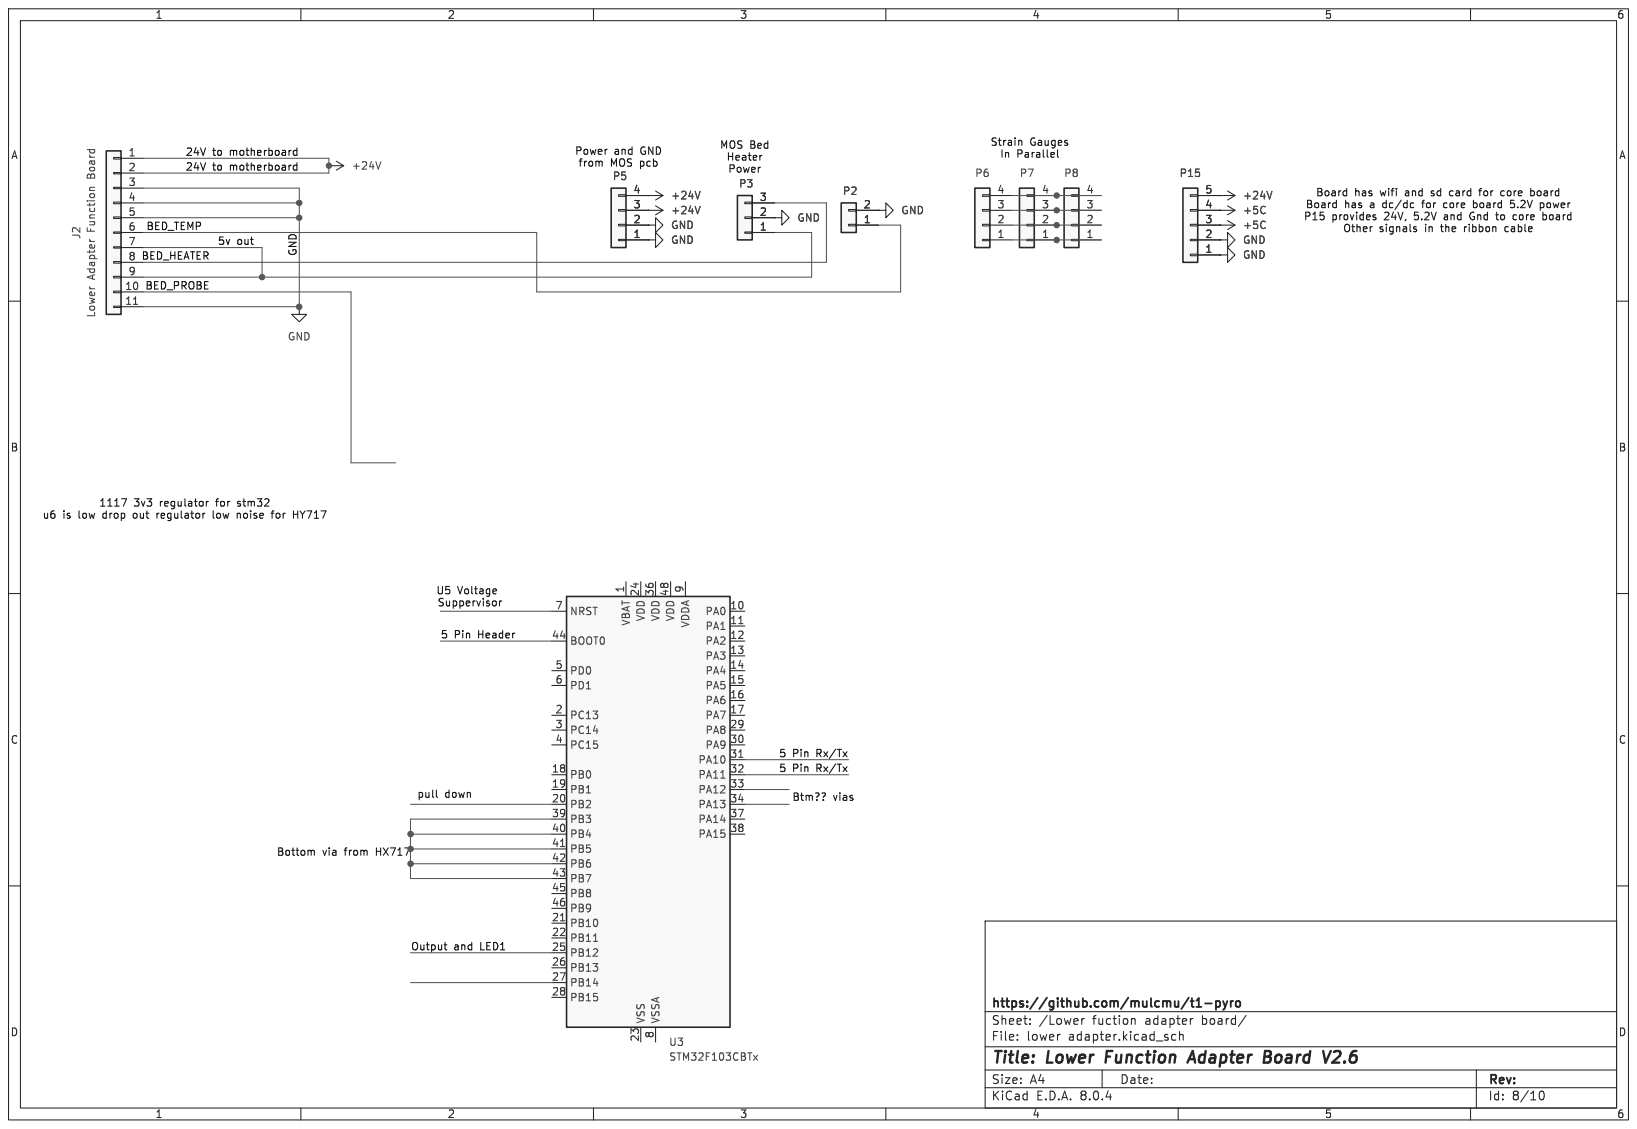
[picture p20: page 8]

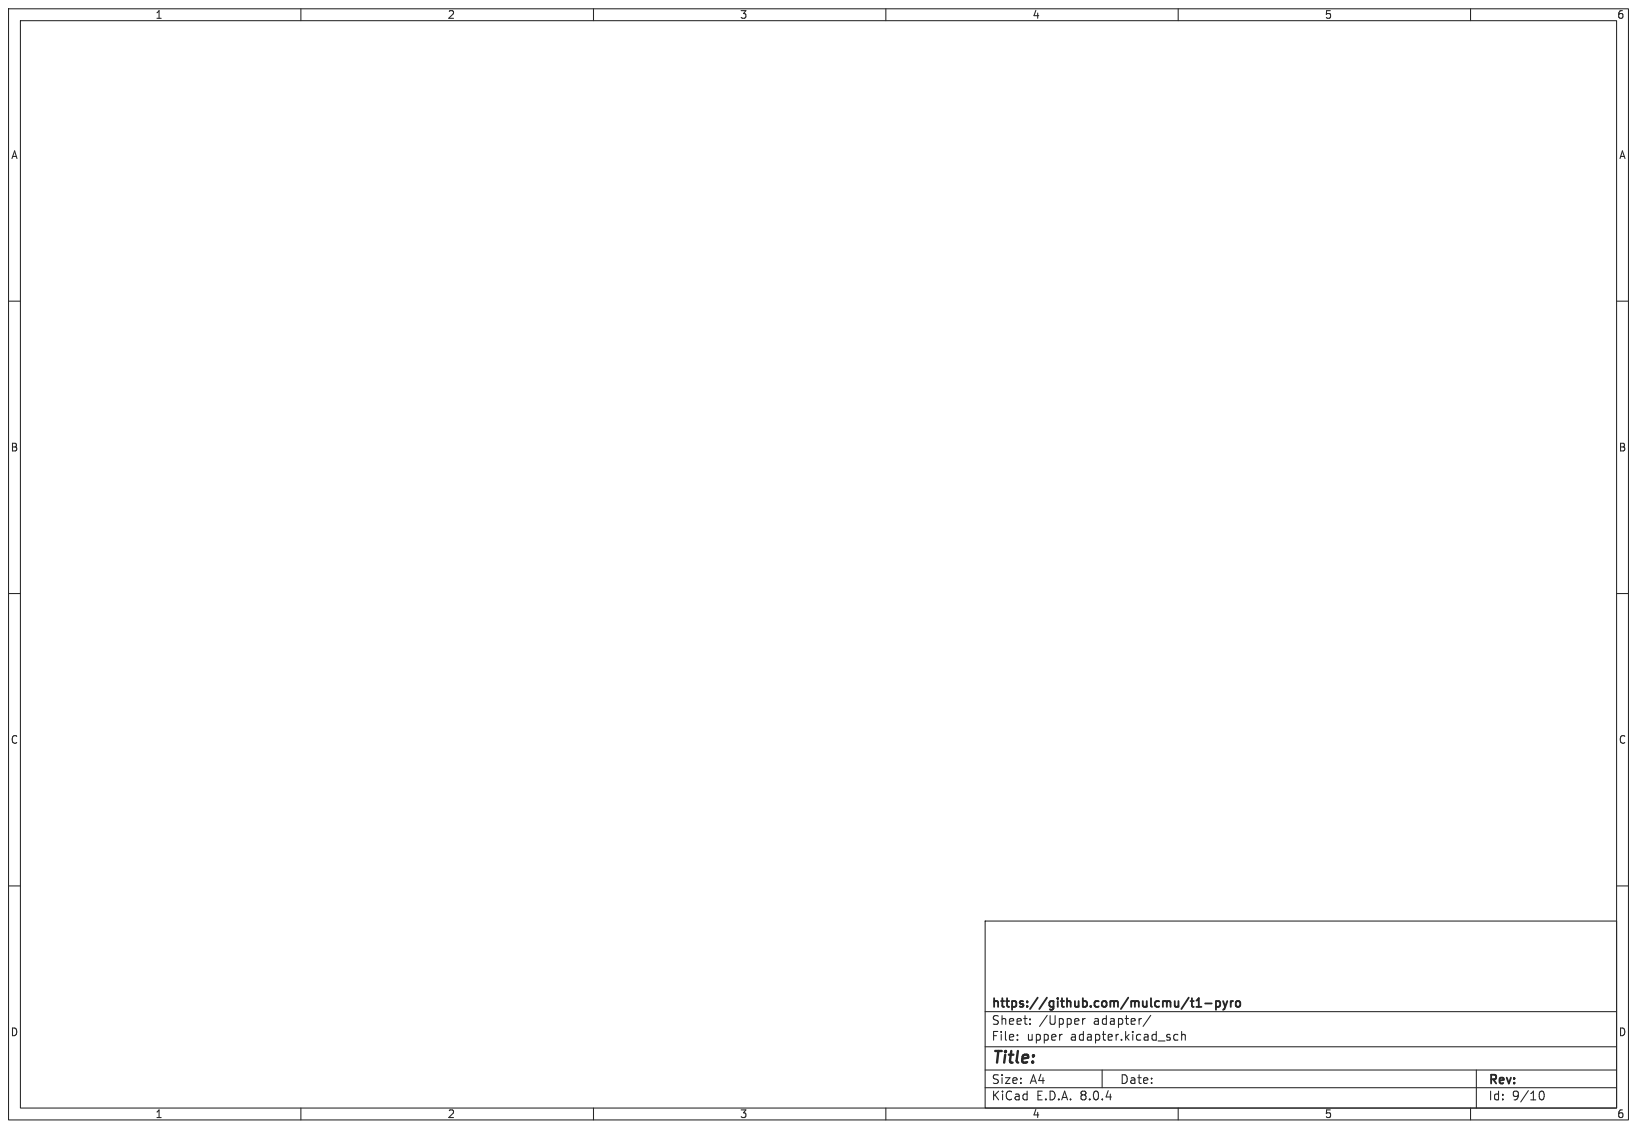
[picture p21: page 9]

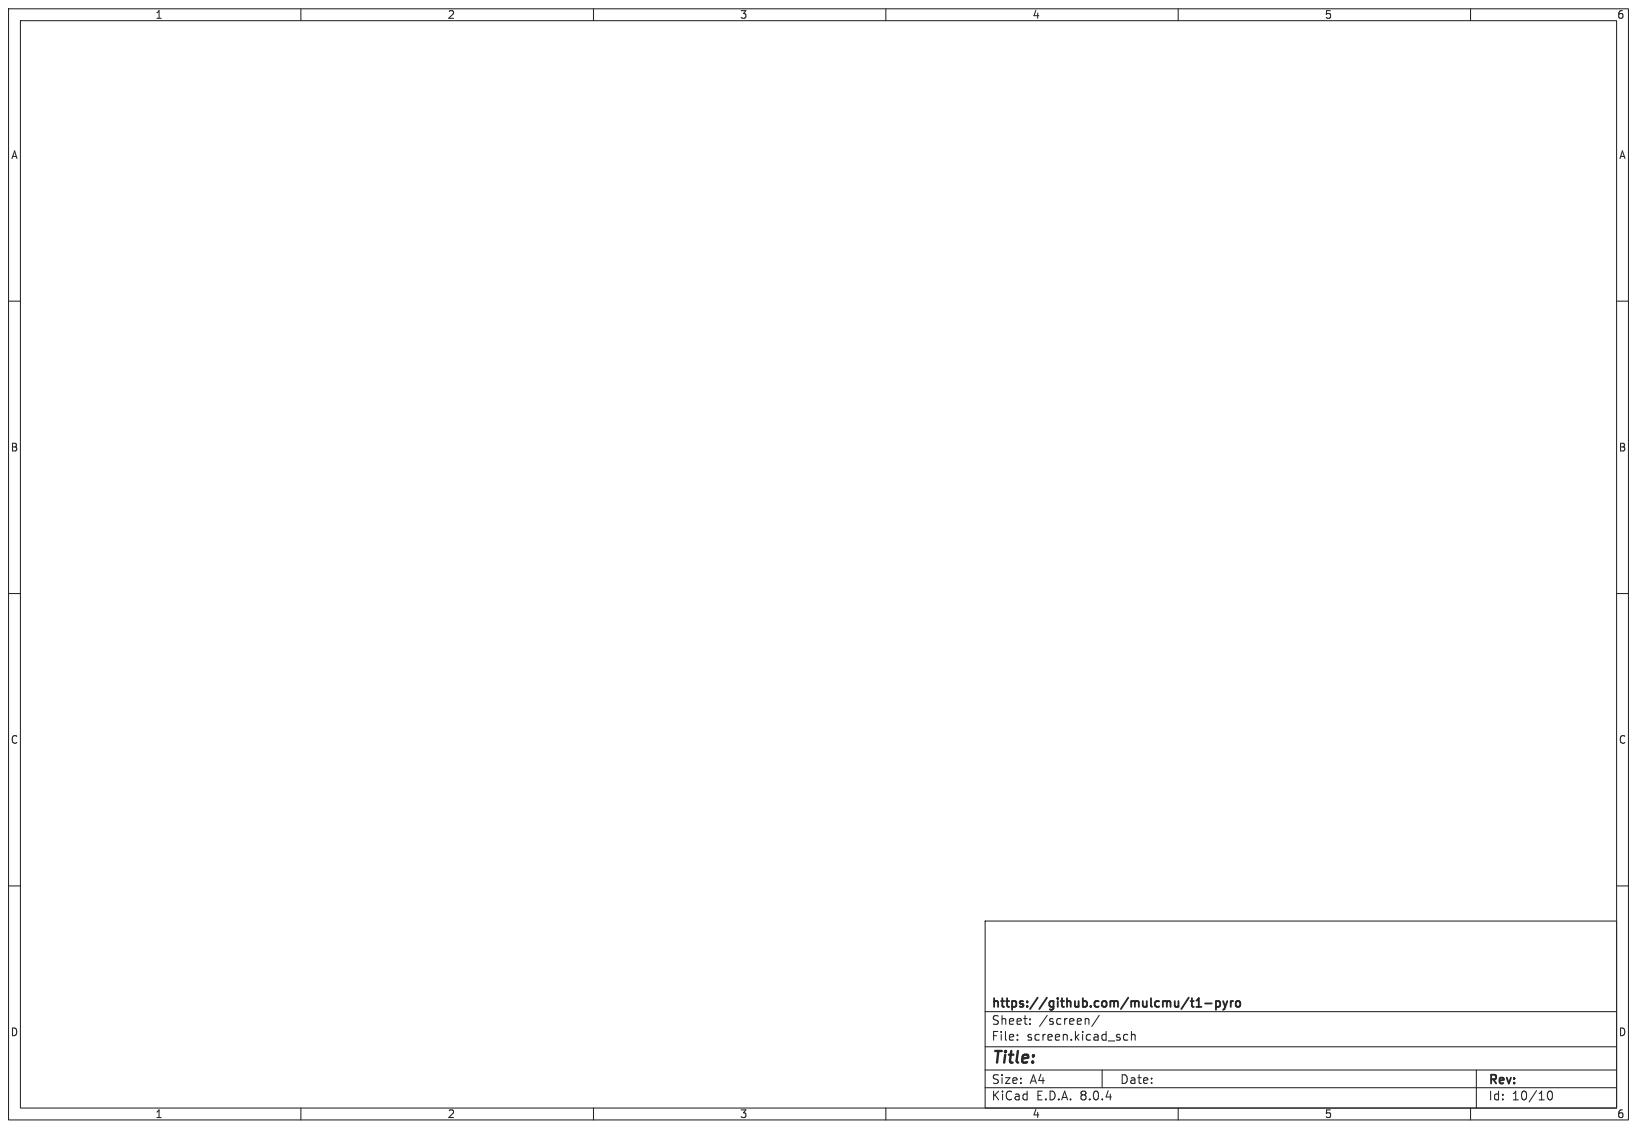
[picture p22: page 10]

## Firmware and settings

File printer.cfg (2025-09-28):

#T1Pro

[include shell_command.cfg]

[include mainsail.cfg]

[include timelapse.cfg]

[mcu]
serial: /dev/serial/by-id/usb-1a86_USB_Serial-if00-port0
restart_method: command

[mcu host]
serial: /tmp/klipper_host_mcu

[mcu LoadCell]
serial:  /dev/ttyS0
restart_method: command

[endstop_phase]

[load_cell_probe]
sensor_type: hx717
sclk_pin: LoadCell:PB9
dout_pin: LoadCell:PB8
sensor_orientation: inverted
counts_per_gram = 68.54675
reference_tare_counts = 1465556
force_safety_limit: 1000
trigger_force: 75
z_offset: 0.0 #the distance between nozzle and level switch
speed: 2.0
samples: 5 
samples_result: average
sample_retract_dist: 1
samples_tolerance: 0.01
samples_tolerance_retries: 5

#drift_filter_cutoff_frequency: 0.8
#   Enable optional continuous taring while homing & probing to reject drift.
#   The value is a frequency, in Hz, below which drift will be ignored. This
#   option requires the SciPy library. Default: None
# buzz_filter_cutoff_frequency: 100.0
#   The value is a frequency, in Hz, above which high frequency noise in the
#   load cell will be igfiltered outnored. This option requires the SciPy
#   library. Default: None
notch_filter_frequencies: 60
#   1 or 2 frequencies, in Hz, to filter out of the load cell data. This is
#   intended to reject power line noise. This option requires the SciPy
#   library. Default: None
notch_filter_quality: 6.0
#   Controls how narrow the range of frequencies are that the notch filter
#   removes. Larger numbers produce a narrower filter. Minimum value is 0.5 and
#   maximum is 3.0. Default: 2.0
#tare_samples:
#   The number of samples to use when automatically taring the load_cell before
#   each probe. The default value is: sample_per_second * (1 / 60) * 4. This
#   collects samples from 4 cycles of 60Hz mains power to cancel power line
#   noise.
# pullback_distance: 0.2
#   The length of the pullback move. The default is 0.2mm and is a safe
#   starting point for most beds. This can be decreased if the motion system
# is very ridgid
#pullback_speed:
#   The speed of the pullback move. The default value is 1.0 micron per sensor
#   sample. Increasing this value will speed up the move and reduce accuracy.
#tap_buzz_filter_cutoff_frequency: 70
#   Filter out high frequency noise in the probe force data before doing Tap
#   Analysis. Frequencies above this number will be filtered with a
#   Butterworth filter. This option requires the SciPy library. Default: None
#tap_buzz_filter_order: 4
#   This is the order of the Butterworth filter. Higher order numbers
#   increase the complexity of the filter and the sharpness of the cutoff.
#   Default: 4.
# notch_filter_frequencies: 50, 60
#   Filter out specific frequencies of noise in the probe force data before
#   doing Tap Analysis. Up to 6 frequencies may be specified. This
#   option requires the SciPy library. Default: None.
# notch_filter_quality: 2.0
#   Controls how narrow the range of frequencies are that the tap notch filter
#   removes. Larger numbers produce a narrower filter. Minimum value is 0.5 and
#   maximum is 3.0. Default: 2.0
#bad_tap_retries: 1
#   Number of attempts that the probe shoudld make before failing. One retry
#   will cause the probe to be cleaned once and make a second probe attempt.
#   Default: 1

[simple_tap_classifier]
#min_decompression_force_percentage: 66.6
#   Checks that the decompression force is at least 2/3's of the measured
#   compression force. A low decompression force usually indicates plastic oozed
#   out during the dwell time before the pullback move.
#max_baseline_force_change_percentage: 50
#   Checks that the force before and after the tap do not differ by more than
#   50% of the measured compression force. A large difference may indicate the
#   presence of molten plastic under the nozzle or an unstable bed surface.
#compression_start_angle_range: 70, 110
#compression_end_angle_range: 70, 110
#decompression_start_angle_range: 95, 135
#decompression_end_angle_range: 95, 135
#   Checks that the angle measured at each point on the tap graph falls inside
#   the configured range. The range must be 2 values in min, max order and
#   between 0 and 180 degrees.
#   The default for all of these is None.

# [tap_recorder]
# load_cell_probe: load_cell_probe
# #   Specify the name of the load cell probe to listen to.


[printer]
kinematics: delta
max_velocity: 1000 #max print speed ,default is 400mm/s
max_accel: 30000 
square_corner_velocity: 5 
max_z_velocity: 1000
print_radius: 133 #max printable radius
minimum_z_position:-1.05
delta_radius = 171.822312

[stepper_a]
step_pin: PE5
dir_pin: !PD7  
enable_pin: !PE1
microsteps: 32
rotation_distance: 60
endstop_pin: ^PD4
homing_speed: 40
homing_retract_dist: 2.5
second_homing_speed: 2.5
angle = 210.068157
arm_length = 333.541020
position_endstop = 330.546

[stepper_b]
step_pin: PB9
dir_pin: !PC7  
enable_pin: !PD3
microsteps: 32
rotation_distance: 60
endstop_pin: ^PD14
angle = 329.998346
arm_length = 335.415210
position_endstop = 331.930

[stepper_c]
step_pin: PB8
dir_pin: !PE15  
enable_pin: !PD13
microsteps: 32
rotation_distance: 60 
endstop_pin: ^PE10
angle = 90.268900
arm_length = 336.463818
position_endstop = 331.505

[tmc5160 stepper_a]
cs_pin: PB4
spi_software_sclk_pin:PE0
spi_software_miso_pin:PB3
spi_software_mosi_pin:PD5
#spi_speed:100000
sense_resistor: 0.0375
run_current: 3
hold_current: 1.6
stealthchop_threshold: 0
interpolate: true

[tmc5160 stepper_b]
cs_pin: PC6
spi_software_sclk_pin:PD0
spi_software_miso_pin:PA8
spi_software_mosi_pin:PD1
#spi_speed:100000
sense_resistor: 0.0375
run_current: 3
hold_current: 1.6
stealthchop_threshold: 0
interpolate: true

[tmc5160 stepper_c]
cs_pin: PD9
spi_software_sclk_pin:PD10
spi_software_miso_pin:PD8
spi_software_mosi_pin:PD11
#spi_speed:100000
sense_resistor: 0.0375
run_current: 3
hold_current: 1.6
stealthchop_threshold: 0
interpolate: true

[extruder]
step_pin: PD15
dir_pin: !PB0
enable_pin: !PB1
microsteps: 16
rotation_distance: 4.5
nozzle_diameter: 0.400
filament_diameter: 1.750
heater_pin: PA5
sensor_type: Generic 3950
#sensor_type: hotend_hack
pullup_resistor: 510
sensor_pin: PA4
min_temp: -200 # extruder min temp
max_temp: 320 # extruder max temp
max_extrude_cross_section: 50 # default 0.640
max_extrude_only_distance: 500
pressure_advance: 0.025 
#pressure_advance: 0.041
control = pid
pid_kp = 18.049
pid_ki = 0.970
pid_kd = 83.929

[tmc5160 extruder]
cs_pin:PC4
spi_software_sclk_pin:PA7
spi_software_mosi_pin:PA6
spi_software_miso_pin:PC5
sense_resistor: 0.0375
run_current: 1.2
hold_current: 0.3 # motor hold current

[fan]
pin: !PE6
cycle_time: 0.0001
max_power: 0.6
kick_start_time: 0.0

#Implement the hotend fan with hysteresis to avoid rapid on/off cycling
[display_template HEATSINK_FAN]
text:
    {% set temp = printer['extruder'].temperature %}
    {% set speed = printer['fan_generic heat_sink_fan'].speed %}
    {% set set_temp = printer['extruder'].target %}

    {% if temp < 35 and set_temp == 0 %}
        { "0.0" }
    {% elif temp >= 50 or set_temp > 50 %}
        { "1.0" }
    {% else %}
        { speed | round(1) }
    {% endif %}

[fan_generic heat_sink_fan] 
pin: PE8
shutdown_speed: 1.0

#Set heat sink fan to use above template with hysteresis implemented
[delayed_gcode _START_HEATSINK_FAN]
initial_duration: 1.
gcode:
  SET_FAN_SPEED FAN=heat_sink_fan TEMPLATE=HEATSINK_FAN

[heater_bed]
heater_pin: PA2
sensor_pin: PA1
sensor_type: Generic 3950
min_temp: -5
max_temp: 130 #hotbed max temp
control = pid
pid_kp = 76.182
pid_ki = 1.582
pid_kd = 917.041

[temperature_sensor Armv7 mcu] #the temp of pad
sensor_type: temperature_host
min_temp: 10
max_temp: 100

[temperature_sensor mcu_temp] #the temp of mcu
sensor_type: temperature_mcu
min_temp: 0
max_temp: 100

[input_shaper]
#shaper_freq_x: 34.78   # frequency for the X mark of the test model
#shaper_freq_y: 31.68  # frequency for the Y mark of the test model

[filament_switch_sensor effector_switch]
runout_gcode: 
event_delay: 3.0
debounce_delay: 2.0
switch_pin: !PE7

[filament_switch_sensor btt_switch]
pause_on_runout: True
runout_gcode: 
event_delay: 1.0
debounce_delay: 0.5
switch_pin: ^PA13

[filament_motion_sensor btt_motion]
switch_pin: ^PA14
detection_length: 5
extruder: extruder
pause_on_runout: False
runout_gcode:
  M117 Filament encoder runout  
  PAUSE # [pause_resume] is required in printer.cfg

insert_gcode:
  M117 Filament encoder inserted


[delta_calibrate]
radius: 123.5
horizontal_move_z: 5 #This value is related to the lift height of the nozzle during delta_calibrate
Speed: 100

# Probe config  for stock probe setup
# [probe]
# pin: !PA3
# x_offset: 0 
# y_offset: 0 
# z_offset: -0.24 #the distance between nozzle and level switch
# speed: 10
# samples: 4 
# samples_result: average
# sample_retract_dist: 5
# samples_tolerance: 0.15 # precision
# samples_tolerance_retries: 5
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

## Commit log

2025-03-06 config files
    [config.txt, printer.cfg]
2025-03-16 Create t1 πro.jpg
2025-03-23 Update printer.cfg
    Add debounce delay to runout sensor.
    [printer.cfg]
2025-03-23 custom cable documentation
2025-03-23 document custom cables
2025-03-24 Add schematic
    [blcd.kicad_sch, core board.kicad_sch, extruder.kicad_sch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]
2025-03-24 Add initial schematic
    Changed readme to use FLSUN board nomenclature
    [blcd.kicad_sch, core board.kicad_sch, extruder.kicad_sch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]
2025-03-27 schematic in process
    [blcd.kicad_sch, core board.kicad_sch, lower adapter.kicad_sch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]
2025-03-27 Create schematic b&w.pdf
2025-03-29 updates for load cell
    [core board.kicad_sch, lower adapter.kicad_sch, screen.kicad_sch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]
2025-04-11 revamp installation for katapult
    [config.txt, lower adapter.kicad_sch]
2025-04-12 add probe performance data
2025-04-20 sd card led
2025-09-19 Add schematic workflow
2025-09-19 Auto-update schematic PDF [skip ci]
2025-09-20 Update printer configuration: enhance load cell settings and add endstop phase sections fix stepper spi pins
    [printer.cfg]
2025-09-20 Update README.md: mark completed tasks and add new resources for T1 πro project
2025-09-20 Format STL model links in README
2025-09-28 Add hysteresis control for heat sink fan
    Implemented hysteresis control for the heat sink fan to prevent rapid cycling based on temperature thresholds.
    [printer.cfg]
2025-09-28 Update README checklist for hotend thermistor
    Added hysteresis to hotend fan to avoid the rapid on/off when cooling.
